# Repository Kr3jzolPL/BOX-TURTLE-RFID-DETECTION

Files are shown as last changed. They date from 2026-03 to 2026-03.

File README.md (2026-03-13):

# BOX-TURTLE-RFID-DETECTION
Be aware my first language is not english so it might be some errors ! Thanks

This addon add option for box turtle to have RFID Detection in each lane using PN532 Rfid modules
It uses avaiable port on BTIO for passing USB connection to the Rpi Pico for clean setup, it uses database from spoolman

BOM
Important, The mounts for rfid are only compatible Box Turtle 1.1 Trays, won't work with 1.0 without mods

- 1 PN532 Reader per lane
- 1 4 or 8 I2C mux for PICO for splitting PN532 Reader adresses and better wiring it's using Qwicc connectors

- 1 RPI Pico flashed in micropython
  Here link how to do it, https://www.raspberrypi.com/documentation/microcontrollers/micropython.html
  
- Wires
- Type C to Type C or micro cable depends of your pico

# ---------------- Printing ----------------
- Left side middle x3 
- Right side middle x3
- Right side Right side x1
- left side Right side x1
- stemma multiplexer x8 for I2C mux
- PiPicoScrew for pico mount
# -- Wiring section -- 
Connect readers to your mux, use port 0-1-2-3 on mux , the 4-5-6-7 ports if using 8 channel mux doesn't work so be aware
Be sure to switch to I2C mode in your readers

Check if your wires have enough length for each lane !


Connect mux with readers to pico I2C port then pico to rpi via usb

# Download files named 
- bt_rfid.py in Main addon folder
- btrfid.service.txt file
- pn532_i2c.py and main.py in Send to pico folder

Edit bt_rfid.py 
# ---------------- CONFIG ----------------
PICO_PORT = "/dev/pico-nfc"          # <-- adjust port for your pi
BAUD = 115200

The pico port can be find in your printer settings just like in photo



SPOOLMAN = "http://192.168.1.39:7912"  # <-- adjust for your spoolman ip adress 

- Send it to root folder of rpi same as in photo 



- After you did all the steps you will need to ssh to your pi, you can use putty same as me
- When you are connected to your printer you will need to add that service to startup and execute it using

  - python3 ~/bt_rfid.py
  - the module should work now

  You will need to add a rule to execute this module every restart otherwise you will need to turn it manually each time
  - How to do it :
  - Create a service using :
  - sudo nano /etc/systemd/system/bt-rfid.service
  - Paste everything from btrfid.service.txt file
  Save and exit

  Enable and start
- sudo systemctl daemon-reload
- sudo systemctl enable bt-rfid.service
- sudo systemctl start bt-rfid.service

After you did everything mentioned before now you can send main.py and i2c module using mpremote
I have my pico in ACM4 port but your can be different so ajust for your setup

- mpremote connect /dev/ttyACM4 fs cp pn532_i2c.py :pn532_i2c.py
- mpremote connect /dev/ttyACM4 fs cp main.py :main.py
- mpremote connect /dev/ttyACM4 reset

# ---Bind Pico to pico-nfc port---
1️⃣ Plug the Pico and find its current port
ls /dev/ttyACM*

Example output:

/dev/ttyACM4
2️⃣ Get Pico USB identifiers
udevadm info -a -n /dev/ttyACM4 | grep '{idVendor}\|{idProduct}\|{serial}' -m3

Example result:

ATTRS{idVendor}=="2e8a"
ATTRS{idProduct}=="0005"
ATTRS{serial}=="4250304638303305"

Those values identify the Raspberry Pi Pico.

3️⃣ Create udev rule

Open the rules file:

sudo nano /etc/udev/rules.d/99-pico-nfc.rules

Put exactly this (adjust serial if yours is different):

SUBSYSTEM=="tty", ATTRS{idVendor}=="2e8a", ATTRS{idProduct}=="0005", ATTRS{serial}=="4250304638303305", SYMLINK+="pico-nfc"

Save.

4️⃣ Reload rules
sudo udevadm control --reload-rules
sudo udevadm trigger

Done, you have bind the pico to PICO_PORT = "/dev/pico-nfc", use it in bt_rfid.py if not done before

# -- Spoolman Section -- 

In order to communicate with our pico you need to have database and extra section in each spool which is used by our pico 

- To add you will need to add custom section in spoolman settings like in photo, the name need to be same as mine if not it will not work at all
  
When you will be adding your spool in spoolman search on bottom for that external_id section



Here you will need to insert unique id assigned to nfc tag, to do just scan the tag even if not in database and copy the numbers from console in mainsail to that section to assign the "Tag" to that spool 

Then each time you will pass your tag the spool will be assigned to lane 

# -- Assembly section -- 

Assembly each reader same as in photo 



Insert each reader same as in photo between each lane 


Mount the mux in middle of trays, you can use motor mount for mounting 1 screw but if your wires are longer than mine just fix it directly on extrusion, as before connect mux to rpi pico and rpi pico in type c port in BTIO for clean wiring ( Works if you are using CAN not USB for BoxTurtle Motherboard ) , then connect your box turtle as usual and add type c cable from your printer to BTIO type C connector 

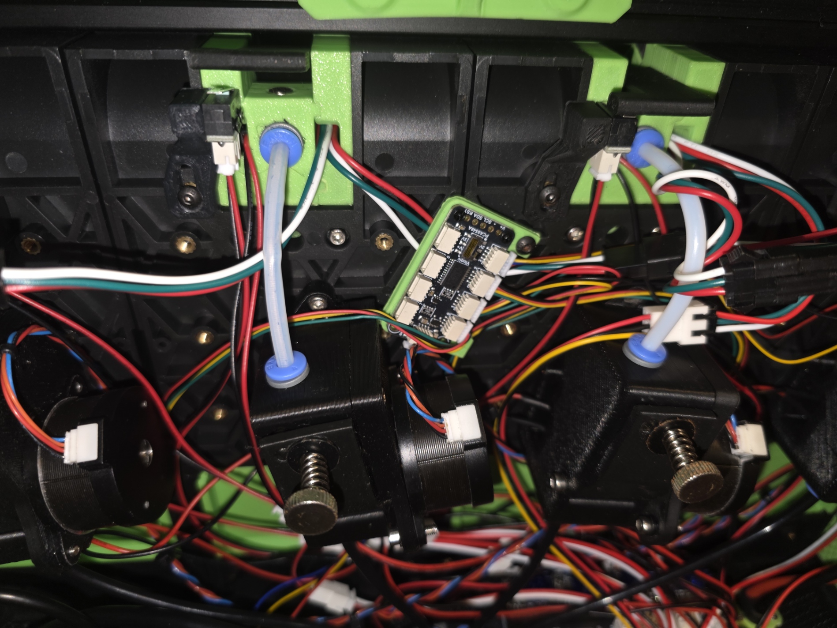
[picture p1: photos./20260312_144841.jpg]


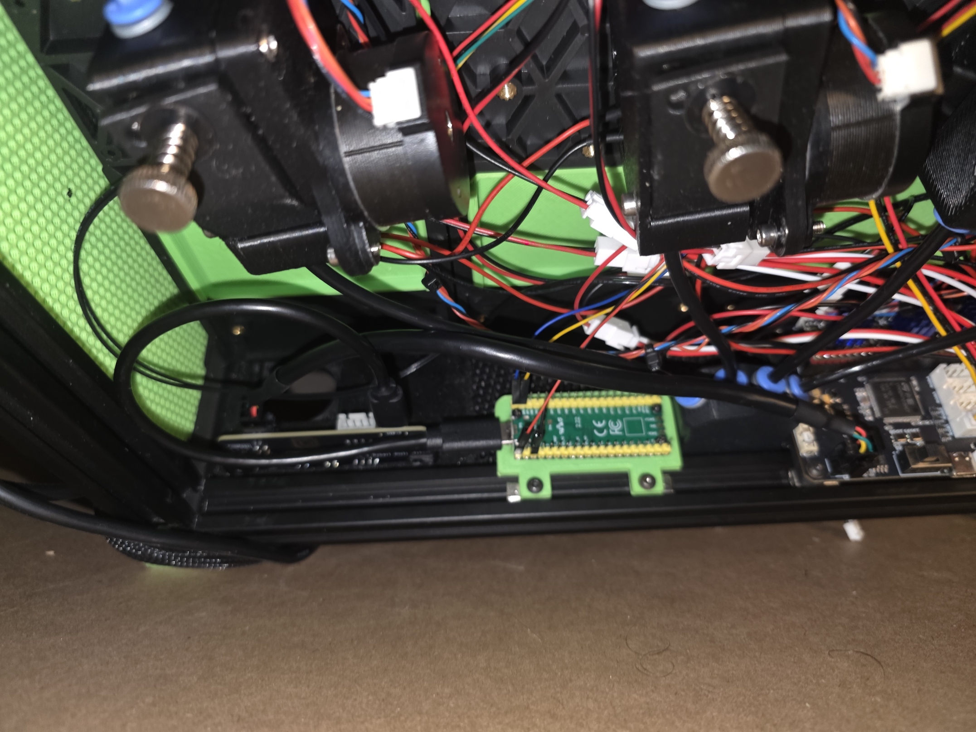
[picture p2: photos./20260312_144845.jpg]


Check if everything works by inserting the spool with tag 

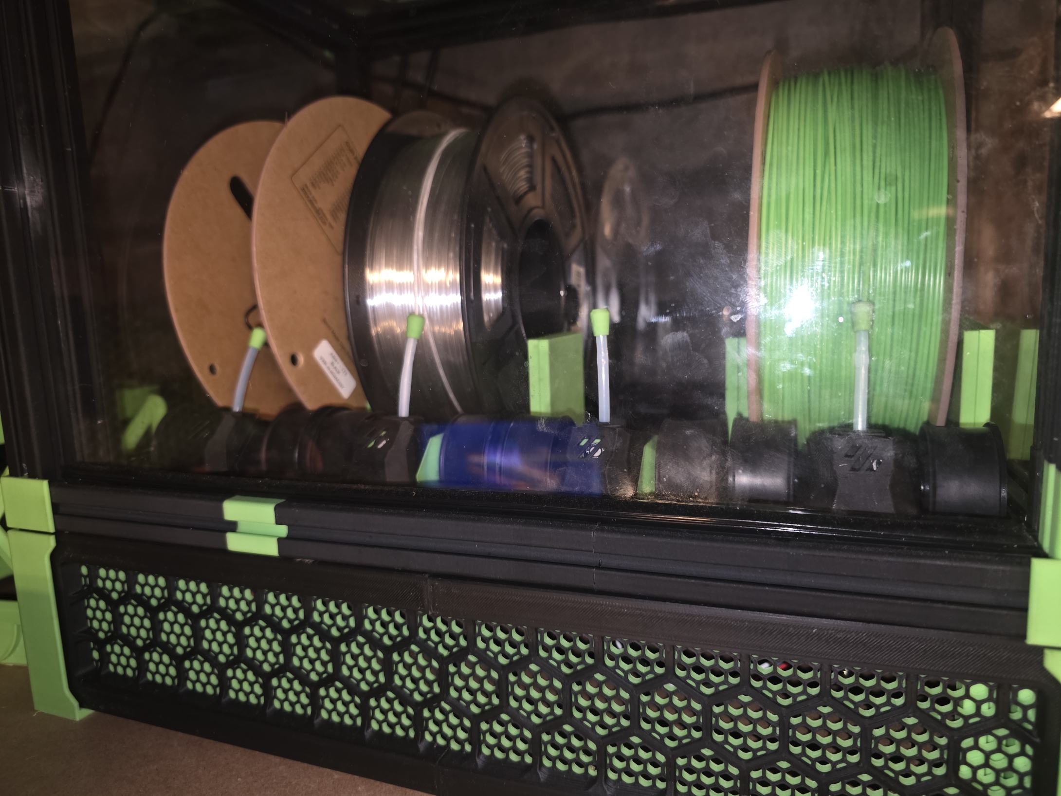
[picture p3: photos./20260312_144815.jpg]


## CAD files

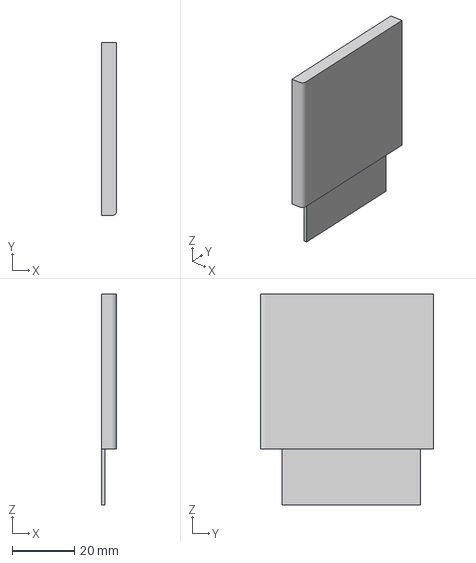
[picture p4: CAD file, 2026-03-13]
mounts/Right Side middle x3 .3mf
4.95 x 55.8 x 68.0 mm

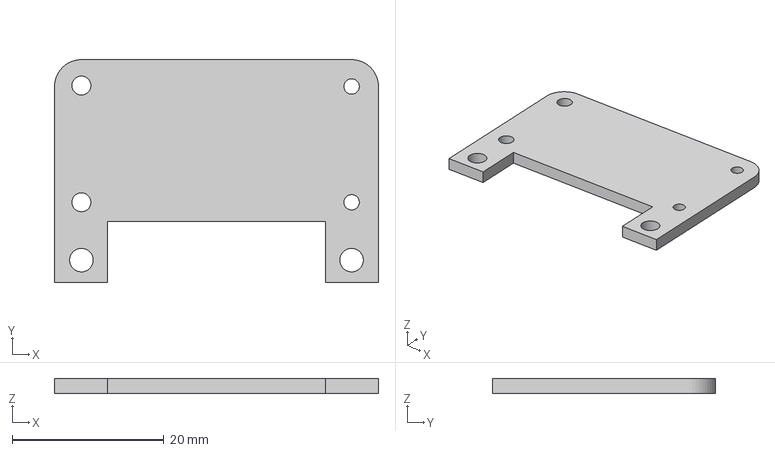
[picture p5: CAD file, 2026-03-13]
mounts/Stemma multiplexer x8 mount extrusion.3mf
42.6 x 29.3 x 2.00 mm

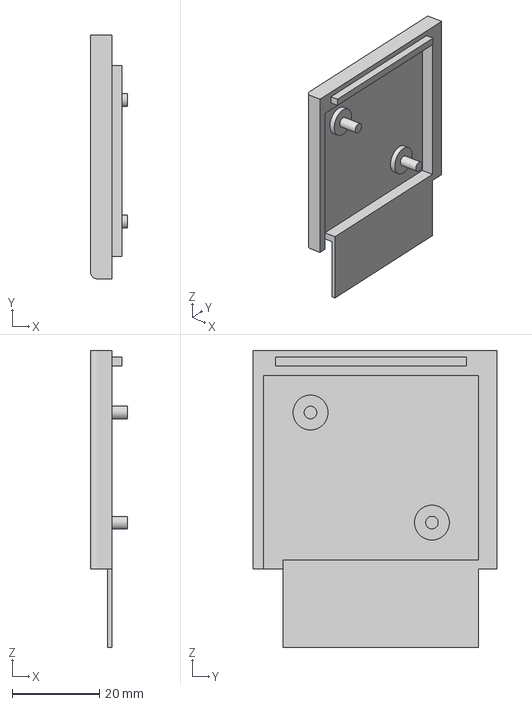
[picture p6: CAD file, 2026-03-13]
mounts/Left side middle x3 .3mf
8.45 x 55.8 x 68.0 mm

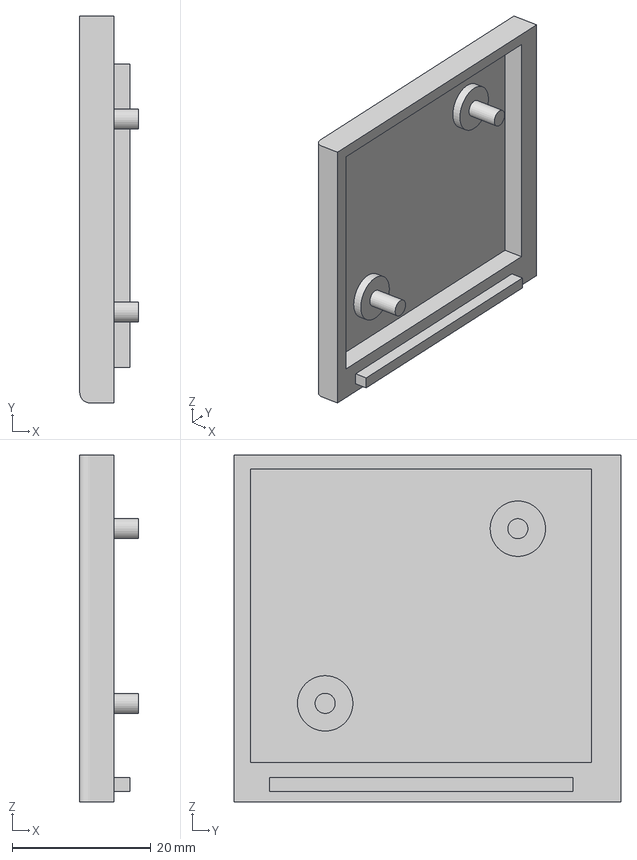
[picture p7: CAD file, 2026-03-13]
mounts/Right side Right side x1 .3mf
8.45 x 55.8 x 50.0 mm

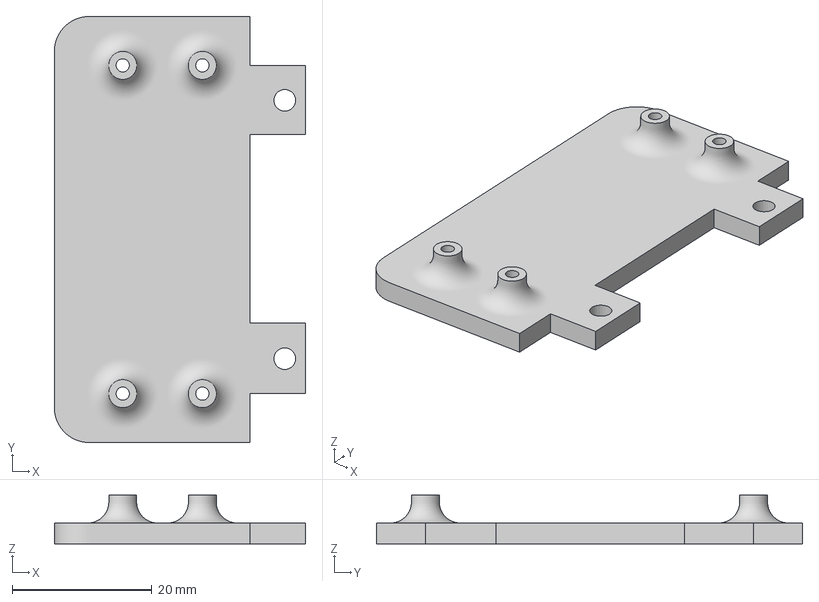
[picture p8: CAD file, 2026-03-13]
mounts/PiPicoW_Screw_Mount.3mf
36.0 x 61.0 x 7.00 mm

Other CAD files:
mounts/left side Right side x1 .3mf

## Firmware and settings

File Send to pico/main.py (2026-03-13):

# main.py - TCA9548A (8ch) + 4x PN532 on channels 0..3
from machine import I2C, Pin
import time
from pn532_i2c import PN532

TCA_ADDR = 0x70
LANE_CHANNELS = {
    1: 3,
    2: 2,
    3: 1,
    4: 0,
}

# Auto "re-arm" when tag disappears for this long
REMOVE_TIMEOUT_MS = 1500

# Pico I2C0 pins (change if needed)
i2c = I2C(0, sda=Pin(0), scl=Pin(1), freq=200_000)

pn = PN532(i2c, timeout_ms=2000)

def mux_select(ch: int):
    # Select one channel (0..7)
    i2c.writeto(TCA_ADDR, bytes([1 << ch]))
    time.sleep_ms(1)

def uid_hex(b):
    return "".join("{:02X}".format(x) for x in b)

# Per-lane state
last_uid = {lane: None for lane in LANE_CHANNELS}
last_seen = {lane: 0 for lane in LANE_CHANNELS}

print("INIT...")

# Initialize each PN532 channel
for lane, ch in LANE_CHANNELS.items():
    mux_select(ch)
    try:
        pn.sam_config()
        # Optional: firmware check (comment out if you don't care)
        # fw = pn.firmware()
        print("READY LANE={} CH={}".format(lane, ch))
    except Exception as e:
        print("INIT_ERR LANE={} CH={} {}".format(lane, ch, e))

print("RUNNING")

while True:
    now = time.ticks_ms()

    for lane, ch in LANE_CHANNELS.items():
        mux_select(ch)

        try:
            uid = pn.scan_uid()
        except Exception as e:
            # Don't spam too hard
            # print("ERR LANE={} {}".format(lane, e))
            uid = None

        if uid:
            last_seen[lane] = now
            # Print only once per insertion / UID change
            if last_uid[lane] != uid:
                last_uid[lane] = uid
                print("LANE={} UID={}".format(lane, uid_hex(uid)))
        else:
            # If we haven't seen a tag for a while, re-arm (allow next detection)
            if last_uid[lane] is not None:
                if time.ticks_diff(now, last_seen[lane]) > REMOVE_TIMEOUT_MS:
                    last_uid[lane] = None

    time.sleep_ms(40)

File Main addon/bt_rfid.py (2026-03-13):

#!/usr/bin/env python3
import re
import time
from typing import Any, Dict, Optional

import requests
import serial

# ---------------- CONFIG ----------------
PICO_PORT = "/dev/pico-nfc"
BAUD = 115200

SPOOLMAN = "http://192.168.1.39:7912"
MOONRAKER = "http://127.0.0.1:7125"

REFRESH_SECONDS = 30
ALLOW_ARCHIVED = True
COOLDOWN_SECONDS = 1.0
# ----------------------------------------

LINE_RE = re.compile(r"LANE=(\d+)\s+UID=([0-9A-F]+)", re.I)

# -------- Printer State Cache --------
_last_state_check = 0
_cached_printing = False


def printer_is_printing() -> bool:
    global _last_state_check, _cached_printing
    now = time.time()

    # Only check once per second
    if now - _last_state_check > 1:
        try:
            r = requests.get(
                f"{MOONRAKER}/printer/objects/query?print_stats",
                timeout=0.5,
            )
            state = r.json()["result"]["status"]["print_stats"]["state"]
            _cached_printing = (state == "printing")
        except Exception:
            _cached_printing = False

        _last_state_check = now

    return _cached_printing


def lane_name(lane_num: int) -> str:
    return f"lane{lane_num}"


def moonraker_run_gcode(script: str) -> None:
    r = requests.post(
        f"{MOONRAKER}/printer/gcode/script",
        json={"script": script},
        timeout=3,
    )
    r.raise_for_status()


def _normalize_external_id(v: Any) -> Optional[str]:
    if v is None:
        return None
    s = str(v).strip()

    while (s.startswith('"') and s.endswith('"')) or (s.startswith("'") and s.endswith("'")):
        s = s[1:-1].strip()

    s = s.upper()
    return s if s else None


def extract_external_id(spool: Dict[str, Any]) -> Optional[str]:
    extra = spool.get("extra")
    if isinstance(extra, dict):
        ext = _normalize_external_id(extra.get("external_id"))
        if ext:
            return ext

    extra_fields = spool.get("extra_fields")
    if isinstance(extra_fields, dict):
        ext = _normalize_external_id(extra_fields.get("external_id"))
        if ext:
            return ext

    if isinstance(extra_fields, list):
        for item in extra_fields:
            if not isinstance(item, dict):
                continue
            name = (item.get("name") or item.get("key") or "").strip().lower()
            if name == "external_id":
                ext = _normalize_external_id(item.get("value"))
                if ext:
                    return ext

    if "external_id" in spool:
        ext = _normalize_external_id(spool.get("external_id"))
        if ext:
            return ext

    return None


def fetch_spool_map() -> Dict[str, int]:
    params = {"limit": 10000}
    if ALLOW_ARCHIVED:
        params["allow_archived"] = "true"

    r = requests.get(f"{SPOOLMAN}/api/v1/spool", params=params, timeout=5)
    r.raise_for_status()
    spools = r.json()

    m: Dict[str, int] = {}
    for s in spools:
        if not isinstance(s, dict):
            continue
        sid = s.get("id")
        if sid is None:
            continue
        ext = extract_external_id(s)
        if not ext:
            continue
        if ext not in m:
            m[ext] = int(sid)
    return m


def main() -> None:
    ser = serial.Serial(PICO_PORT, BAUD, timeout=1)

    spool_map: Dict[str, int] = {}
    last_refresh = 0.0
    last_seen: Dict[int, tuple[str, float]] = {}

    while True:
        now = time.time()

        # Refresh spool map periodically
        if (now - last_refresh) > REFRESH_SECONDS or not spool_map:
            try:
                spool_map = fetch_spool_map()
                last_refresh = now
            except Exception as e:
                try:
                    moonraker_run_gcode(
                        f'ReSPOND PREFIX="NFC" MSG="Spoolman refresh error: {e}"'
                    )
                except Exception:
                    pass
                time.sleep(2)

        line = ser.readline().decode(errors="ignore").strip()
        if not line:
            continue

        m = LINE_RE.search(line)
        if not m:
            continue

        # 🔒 Ignore RFID silently during active print
        if printer_is_printing():
            continue

        lane_num = int(m.group(1))
        uid_hex = m.group(2).strip().upper()
        lname = lane_name(lane_num)

        prev = last_seen.get(lane_num)
        if prev and prev[0] == uid_hex and (now - prev[1]) < COOLDOWN_SECONDS:
            continue
        last_seen[lane_num] = (uid_hex, now)

        spool_id = spool_map.get(uid_hex)

        if spool_id is None:
            try:
                spool_map = fetch_spool_map()
                last_refresh = time.time()
                spool_id = spool_map.get(uid_hex)
            except Exception:
                spool_id = None

        if spool_id is None:
            moonraker_run_gcode(
                f'ReSPOND PREFIX="NFC" MSG="No spool found with external_id={uid_hex} (lane={lname})"'
            )
            continue

        moonraker_run_gcode(f"SET_SPOOL_ID LANE={lname} SPOOL_ID={spool_id}")
        moonraker_run_gcode(
            f'ReSPOND PREFIX="NFC" MSG="Set {lname} -> SPOOL_ID {spool_id} (external_id={uid_hex})"'
        )


if __name__ == "__main__":
    main()

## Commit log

2026-03-13 Create stl
2026-03-13 Rename Left side middle.3mf to Left side middle x3.3mf
    [Left side middle x3.3mf]
2026-03-13 Rename Right Side middle.3mf to Right Side middle x3 .3mf
    [Right Side middle x3 .3mf]
2026-03-13 Rename Right side Right side .3mf to Right side Right side x1 .3mf
    [Right side Right side x1 .3mf]
2026-03-13 Rename left side Right side .3mf to left side Right side x1 .3mf
    [left side Right side x1 .3mf]
2026-03-13 Rename Left side middle x3.3mf to Left side middle x3 .3mf
    [Left side middle x3 .3mf]
